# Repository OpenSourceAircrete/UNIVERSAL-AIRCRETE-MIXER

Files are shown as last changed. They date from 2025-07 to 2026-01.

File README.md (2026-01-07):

# Open Source Aircrete Production Equipment

## Project Overview

*Please donate to the GofundMe* https://www.gofundme.com/f/aircrete-is-awesome?lid=wmmfu28o9xfl

*Here's some research I authored regarding regulatory approval for aircrete. https://www.ijrtmr.com/archives/paper-details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

This repository contains a collection of open-source equipment designs  to produce **Non-Autoclaved Aerated Concrete (NAAC)**, also known as cellular concrete, or "aircrete". https://www.designingbuildings.co.uk/wiki/Aircrete In this context, "low-rate" refers to production volumes suitable for small construction crews constructing or repairing parts of a single home.

https://www.youtube.com/watch?v=HfUKHgh9K9g

https://youtu.be/HfUKHgh9K9g

[url=https://flic.kr/p/2rQEY1Z][img]https://live.staticflickr.com/65535/55028406249_091fecc333_b.jpg[/img][/url][url=https://flic.kr/p/2rQEY1Z]12 inch newbuild wall design (4)_page-0001[/url] by [url=https://www.flickr.com/photos/203763990@N08/]Michael OLeary[/url], on Flickr





PURPLE (1)

The primary focus is on developing modular, portable, and low-volume mixing and pumping equipment. The designs are ideal for "dry bag" mixing operations. To clarify, a "dry bag" mixer performs two critical steps in NAAC production: mixing a Portland cement slurry, and mixing stable foam into that slurry to create NAAC material. This equipment should be robust enough for rental fleets. These designs are intended for community-driven development and collaboration.

It is the designer's belief that NAAC is an ideal residential building material that has been held back by expensive mixing equipment. Ai. There's never been good small contractor grade equipment, with the cheapest good mixers costing $50,000+. The UAM BOM is estimated to be less than $5,000. The two key design features that allow this is the use of 3mm (10 guage) plate and 1/8" tubing in place of 5mm and 1/4" steel and tubing. The designer proved with the alpha protoype that this lighter material is suitable for mixing an end product with a density of 0.6-0.8 (relative to H2O). Reinforced cement concrete, for reference exhibits a 2.4 density. 

*This is exactly what we need the machine to do and an example of the cheapest/best home that can be built.* https://www.youtube.com/watch?v=HfUKHgh9K9g

The mixers have been designed with integrated transfer pumps made from mild steel solid augers. This is a low tech/high capability setup that saves thousands on the BOM. 

A small venturi dust extraction system should shield operators from excessive cement dust. 

Designer's note on the challenges this machine faces: There are three crucial processes a machine like this performs. First it needs to mix a Portland cement slurry. Then it needs to mix in stable foam to produce the NAAC material. Then it needs to transfer the NAAC material out of the machine and over a lightweight wall form. The challenge is this: the first evolution requires "shear force" to properly mix the slurry and hydrate the Portland cement properly. The second and third evolutions must avoid shear force, instead relying on laminar flow to avoid damaging the stable foam. The use of the transfer pump plays a crucial role in this. Manipulating the two 3" "recirculation and discharge" system ball valves to create backpressure should help to shear the slurry. Once the stable foam is starting to be injected the operator will upen the valves wide and eliminate the shear. 

---

## Equipment Designs

The following designs are available for use, modification, and further development. They are listed in order of development priority.

### 1. "Tin Can" Ribbon Mixer and integrated recirculating and transfer pump. 

A modular and lightweight cellular concrete mixer designed for scalability and ease of use.

* **Key Features:**
  * **Ribbon Auger Mixing System:** Features songle ribbon auger (rotating approx. 60 RPM) to ensure thorough and rapid homogenization of the material. The positive recirculating pump assists in mixing effectively lowering the demand on the auger ribbons.
  * **Integrated Solid Impeller Recirculating and Transfer Pump** A "low shear" transfer pump is needed to lift the fully mixed NAAC 4M. That's the expected height of a single story wall forms. The solid impeller, positive displacement transfer pump is also turning at 40-50 RPMS. If NAAC is required to be pumped to a second story the machine should be set up there. 
  * **Clean Mixing Chamber:** The outer auger flight is equipped with rubber wipers on its flights to keep the mixer walls clean and prevent material buildup.
  * **Scalable Volume:** The mixing capacity can be easily scaled by adjusting the length of the mixer's final dimensions.
  * **Adaptable Power:** Can be adapted to various power transmission systems, with a hydraulic setup recommended for its versatility in powering auxiliary equipment and suitability for low RPM operation. 
  * **Portable Design:** Engineered for on-site portability and ease of use. Quick assembly and disassembly allows this machine to be loaded and unloaded out of the back of a standard pickup truck with no overhead lifting gear or a forklift. As such it doesn't need to be traillered. This level of portability as it lowers cost and increases access.

* **Recommended Modifications** This design can be easily modified to save costs in two ways: 1.Upper mixer shell can be fabricated as straight sides rather than a curve. This might result in a decrease in mixing effeciency as the can shape forces the material against the auger flights. 2. Transfer pump can be eliminated. This limits the machine's practicality in almost any operational environment but saves cost on the parts required to build the pump. In a small blockmaking setting transfer pumps seem to be seldom used so this might prove to be popular. 

---

## How to Contribute

This is a community-driven project, and contributions are highly welcome. You can help by:

* **Donating to the GoFundMe: https://www.gofundme.com/f/aircrete-is-awesome?lid=wmmfu28o9xfl

* **Email me at MIKEOLEARY100@GMAIL.COM if you want to help in some way. I am working solo on this and could use the help. 

* **Reviewing the Designs:** Analyze the existing CAD files and drawings for potential enhancements.
* **Suggesting Ideas:** Open an **Issue** to propose new features or modifications.
* **Improving the Designs:** Fork the repository, implement your changes, and submit a **Pull Request**.
* **Investigating Certifications:** A key area for contribution is researching safety standards, such as potential **UL certification requirements related to static electricity** for the Cloud Inhaler.
* **Building and Testing:** Real-world feedback is invaluable. Share your results, documentation, and findings with the community.

## License

This project is dedicated to the public domain under the  CERN-OHL-P

Full text available here: https://ohwr.org/cern_ohl_p_v2.txt

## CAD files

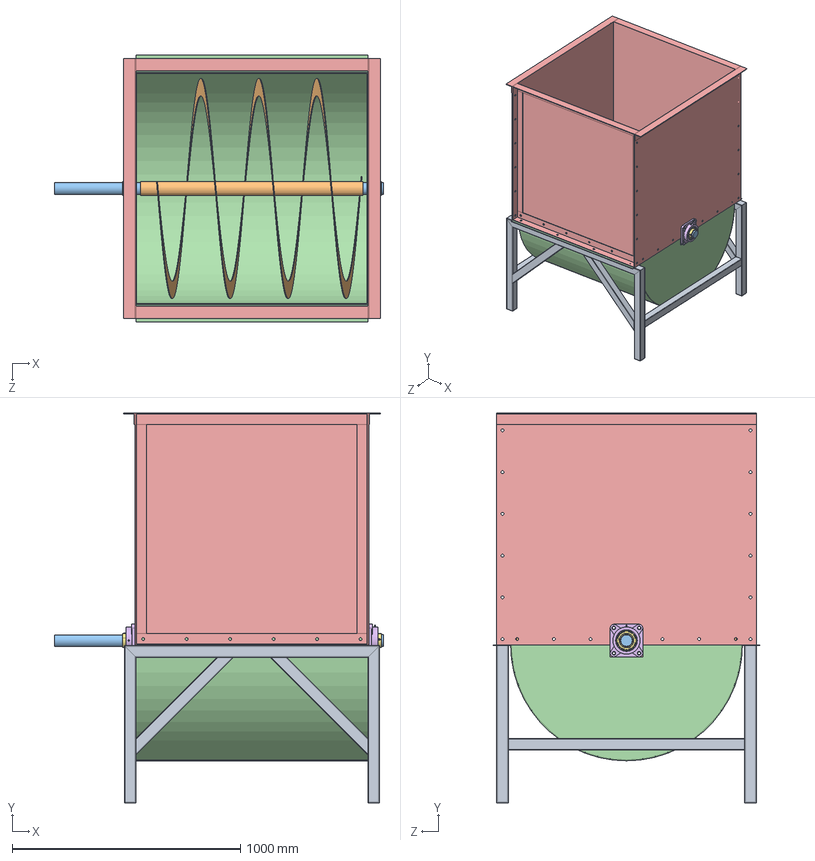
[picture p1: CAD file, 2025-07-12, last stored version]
1_ Half Pipe/CAD files/SolidWorks/General Assembly (1).SLDASM
1443.0 x 1708.8 x 1168.4 mm
Support
Tube axis
Free axis x 2
Tank
top box
f_210 x 2
UC210_3D.stp x 2

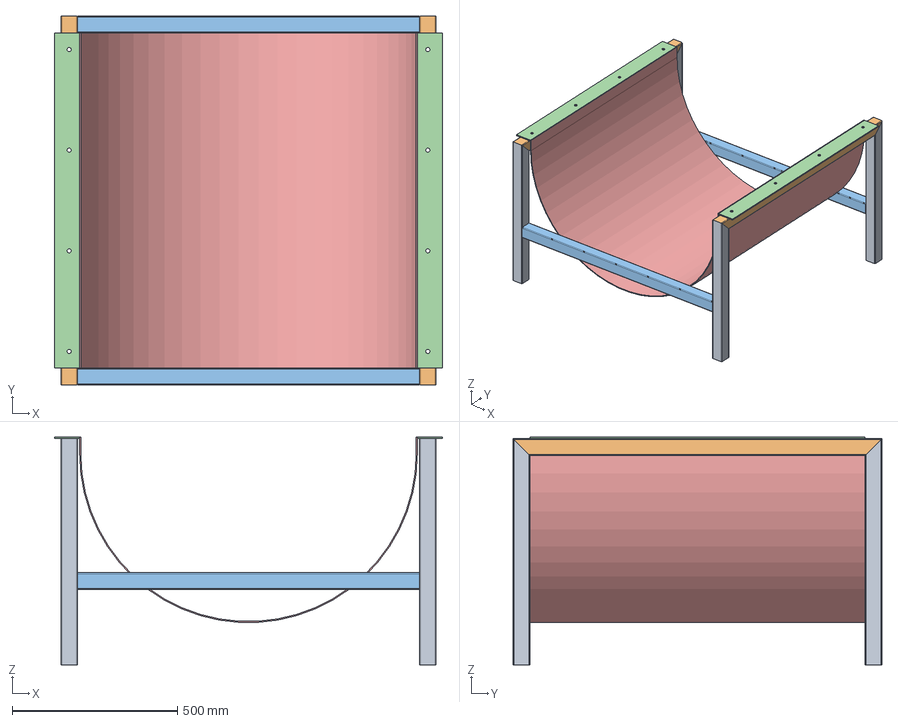
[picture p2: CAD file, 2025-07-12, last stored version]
1_ Half Pipe/CAD files/FreeCAD/Air Crete Project (2).FCStd
1175.4 x 1117.6 x 690.6 mm
SL_BODY x 4
SCM_BODY x 2
SCB_BODY x 2
LTW_BODY x 2
LT_BODY

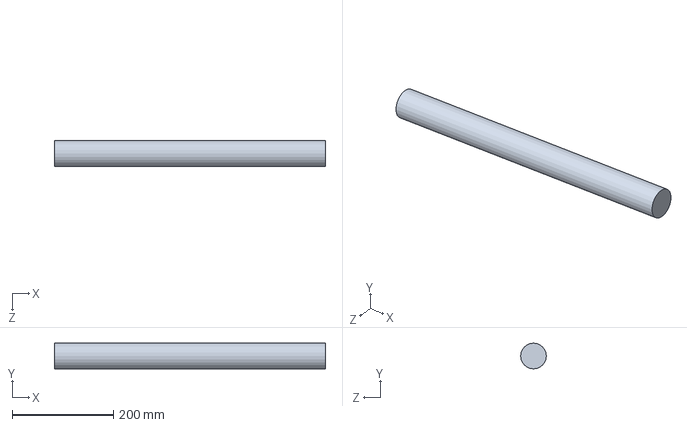
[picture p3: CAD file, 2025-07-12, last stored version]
1_ Half Pipe/CAD files/SolidWorks/Free axis (1).SLDPRT
535.0 x 50.8 x 50.8 mm

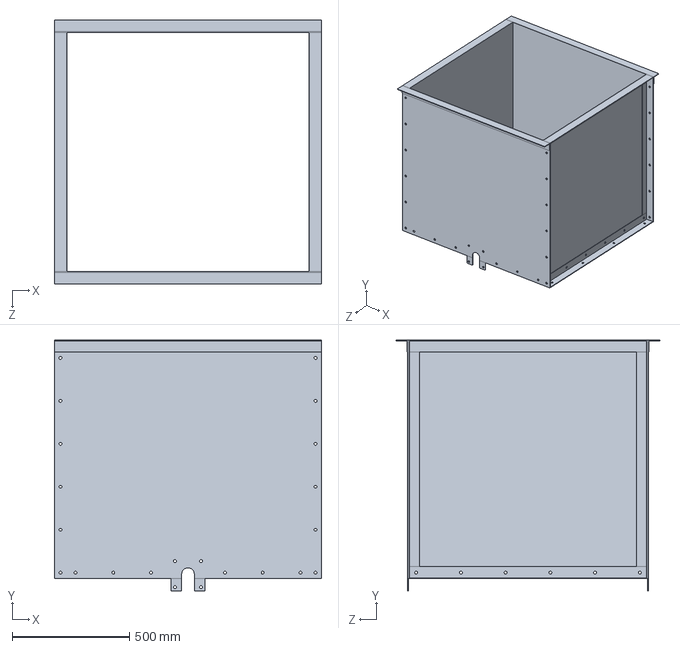
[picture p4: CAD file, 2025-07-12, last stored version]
1_ Half Pipe/CAD files/SolidWorks/top box (1).SLDPRT
1137.3 x 1068.4 x 1126.1 mm

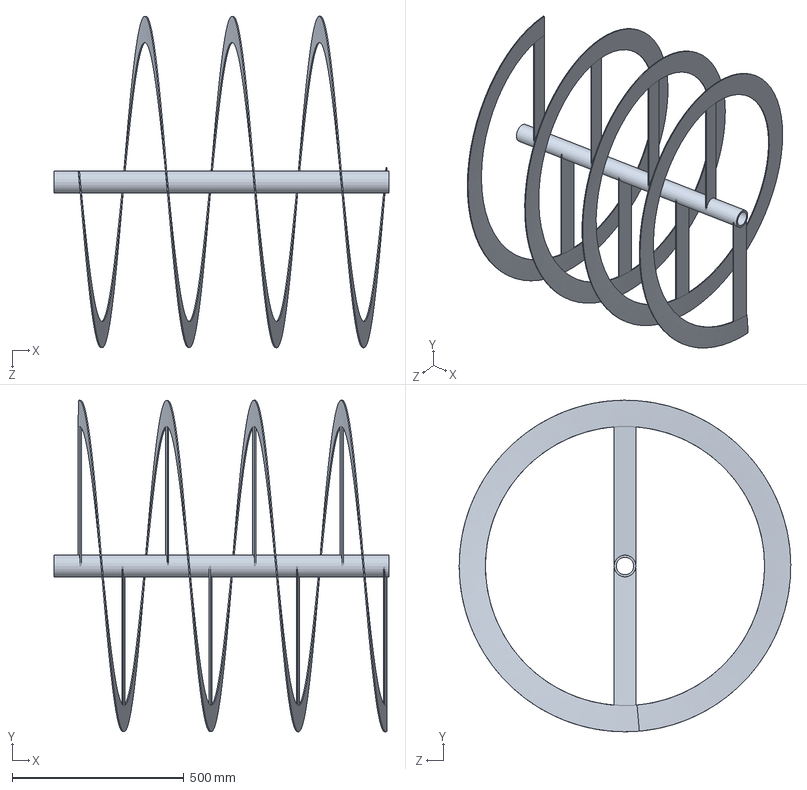
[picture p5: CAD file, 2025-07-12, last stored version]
1_ Half Pipe/CAD files/SolidWorks/Tube axis (1).SLDPRT
975.0 x 965.2 x 965.2 mm

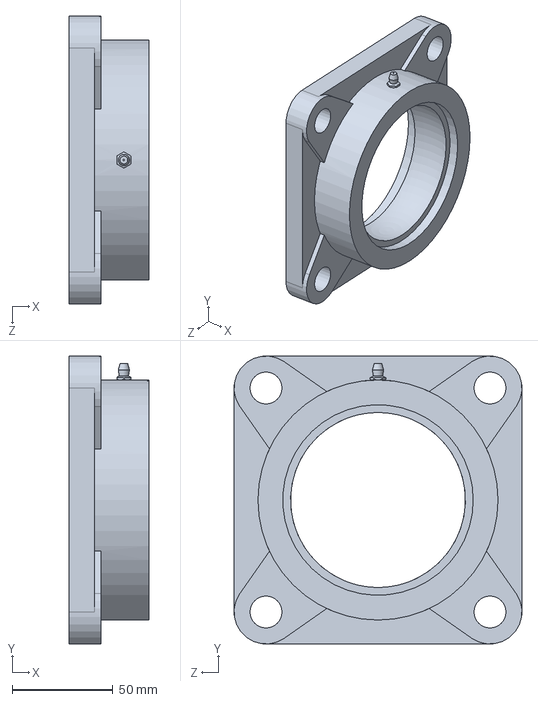
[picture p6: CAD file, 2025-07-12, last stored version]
1_ Half Pipe/CAD files/SolidWorks/Mancal (1).SLDPRT
39.7 x 142.9 x 142.9 mm

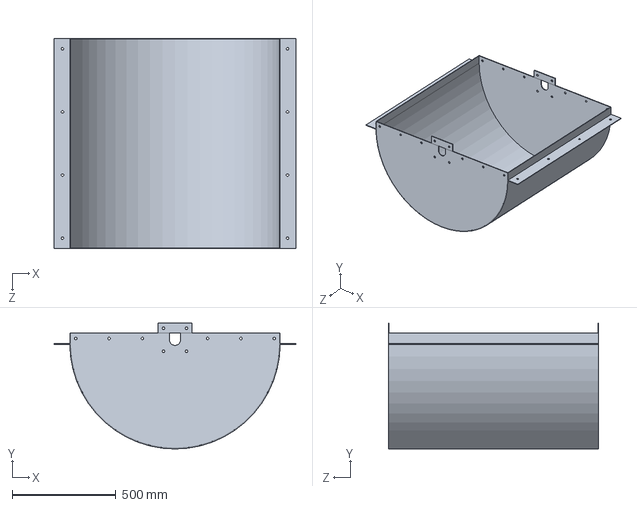
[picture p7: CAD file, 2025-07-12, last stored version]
1_ Half Pipe/CAD files/SolidWorks/Tank (1).SLDPRT
1168.4 x 608.0 x 1016.0 mm

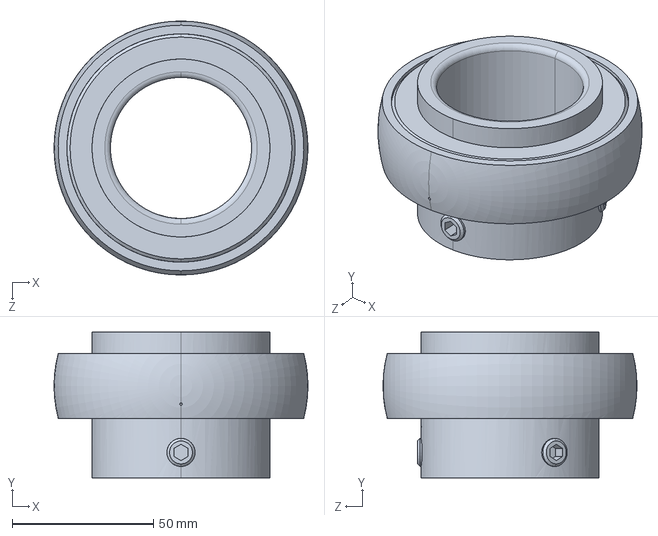
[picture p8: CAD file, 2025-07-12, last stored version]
1_ Half Pipe/CAD files/SolidWorks/UC210_3D.stp (1).SLDPRT
90.0 x 51.6 x 90.0 mm

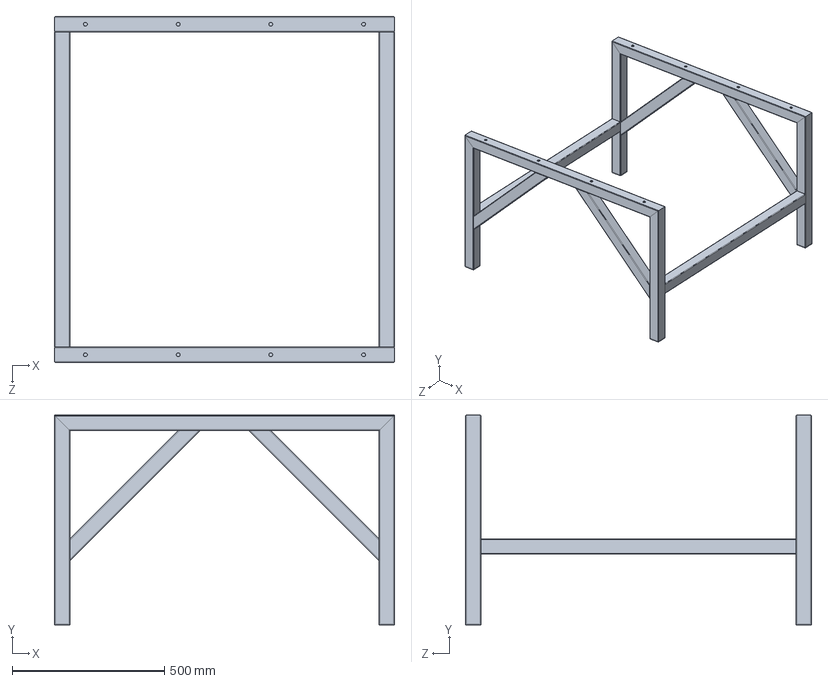
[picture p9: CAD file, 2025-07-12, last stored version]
1_ Half Pipe/CAD files/SolidWorks/Support (1).SLDPRT
1117.6 x 689.3 x 1137.3 mm

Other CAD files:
1_ Half Pipe/CAD files/SolidWorks/General Assembly (1).SLDDRW

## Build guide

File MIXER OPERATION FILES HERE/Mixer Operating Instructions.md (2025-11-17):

UAM Operating Instructions

Make sure recirc valve is open then check discharge valve is closed. Add fresh water via the water transfer system by lining up valves correctly and ensure that the required amount of water is in the mixer by checking the “innage line” on the inside of the tank. Turn on the air “fluidizer valve”. That will prevent cement from clogging the sump as you add it. Turn on the dust extraction system. The fresh water 

Add 1 bag of Portland cement. Shouldn’t have to be too careful. Just dump it in. Wait 30 seconds and add another bag of Portland cement. Make sure to document time this step is done. Add any admixture and document that too.

When the cement slurry is well blended start the foam generator by first opening the air valve to the chamber. Open the “foam sample valve” and then line up the valves on the water transfer system to discharge soapy water solution to the foam generator. Stable foam should soon be discharging out of the “foam sample port”. 
Check the appearance of the foam and weigh it to check density. If too dense open the air supply needle valve on the foam chamber. If not dense enough, close the same valve. When satisfied the foam is the correct weight in the sample container, indicating it’s density, open the “foam discharge valve”, then close the “foam sample valve”  to the mixing vessel and start mixing. 

Watch the innage marks on the “soapy water tank. When the level gets close to the mark, start weighing the mixed aircrete material by collecting samples via the “aicrete sample port”

When the aircrete is the correct density stop the foam generator by turning off the water transfer pump, then shut the water valves, then shut the air going to the foam generator (ball valve).

Have the second operator walk the aircrete transfer hose over to the forms. The machine operator should then open the aircrete transfer valve all the way, then slowly “pinch down” on the recirc valve until the material is flowing out of the transfer hose at the right rate. This continues until the tank is empty of aircrete material. 

When the tank is empty close the recirc valve to 25%. Carefully open “Purge valve 1” a little, with a bucket hanging beneath the pipe fitting. That will let air “bleed out” of the line and some material will flow into the bucket as the pump “picks up” air and material alternating as the mixing vessel and sump are dry. 

By now there is only aircrete in the end of the pump and the discharge pipe. After about 10-15 seconds of this close purge valve 1. 

Quickly open the recirc all the way and then close the discharge all the way. That will trap the material above the discharge valve and avoid “deadheading” the pump (a bad idea for a positive displacement pump…if you deadhead this at the wrong time you will break something probably…for sure the noise will scare you). 

Open up “Purge valve #2”. With the aircrete transfer valve closed the purge air will push against it and force the remaining aircrete up and out of the hose. This last material will have irregular air pockets and should be used in a non critical area. 

Open the “pump drain valve” to get all the material out of the vessel from the lowest point, assisted by the pump. Collect it in a bucket. Document the time the batch was finished dicharging.

Use the water transfer system to put 5-10L into the mixing vessel and recirculate it to clean it out prior to the next batch. When doing this cycle the aircrete discharge valve to prevent material buildup.

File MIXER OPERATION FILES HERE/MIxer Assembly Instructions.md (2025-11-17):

Universal Aicrete Mixer Assembly instructions

 Pull major parts of UAM out of truck bed or trailer.

Place leg unit in operating area and lift lower tank shell into place.

Place auger assembly into lower tank shell. 

Fit bolts into bearing mounting plate holes. Check alignment of auger flights with bottom and sides of lower tank shell with spacer shims and then tighten bearing plate mounting bolts. 

Fit gasket on tank shell flange, keeping hole cutouts aligned. 

Place upper tank shell into place. 

Fit chain around mixer and transfer pump sprockets. 

Use flat blade screwdriver or small pin bar to align holes. Be careful to not damage gasket. 

Fit bolts loosely into tank shell flange bolt holes and once all are in loosely, snug them in a “star pattern” so the flanges seat the gasket well. 

Bolt transfer piping flanges together in 2 places: pump discharge location (discharge line) and tank top location (recirc line).  

Bolt power transmission mounting plate to motor bench, fitting gear reduction shaft coupling to coupling on auger shaft.

Bolt foam generator to front bench. Foam generator consists of water transfer pump, water manifold, air manifold, and foam chamber (3” pipe with steel wool). 

Connect water line from fresh water tank and premixed soapy water tank to the water manifold. 

Bolt air compressor to front bench. Connect compressor air discharge line to air manifold. 

Connect foam generator discharge line to mixing vessel connection via 2” camloc. 

Connect material transfer hose to pump discharge. 

Test run the mixer/pump: Make sure the transfer valves are open. Make sure workers are clear of machine and turn the motor on to see if the auger and pump are turning freely and machine looks and sounds OK. You are looking for any excess shaking or vibration. You are listening for excess scraping or unusual noises. Note: Starting the machine is the most important time to pay attention to it. 

      Leaving the recirc valve open, close the discharge valve. Pour 5 gallons of fresh water into the mixer and recirculate only. Check for rate out of the recirc line discharge location at the top of the mixing vessel and listen for noises that would indicate an obstruction. Watch the discharge pressure gauge as that will also signal a problem by showing excess “backpressure” (discharge pressure the transfer pump is working against). 

If the machine looks and sounds OK recirculating the 5 gallons of water, put in 7 more gallons. You are now ready to mix aircrete.

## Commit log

2025-07-10 Add initial project structure and configuration files
    [Air Crete Project (2).FCStd, Free axis (1).SLDPRT, General Assembly (1).SLDDRW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]
2025-11-16 Create CAD FILES HERE
2025-11-16 Update CAD FILES HERE
2025-11-16 Create Cad Files
2025-11-16 Update Cad Files
2025-11-16 Create Assembly Instructions
2025-11-17 Create CAD FILES.md
2025-11-17 Create MIxer Assembly Instructions.md
2026-01-07 Create Integrated wall CAD files
2026-01-10 Create Integrated shear wall CAD files
